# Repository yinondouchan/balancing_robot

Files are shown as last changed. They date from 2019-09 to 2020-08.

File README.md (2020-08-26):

# balancing_robot
A balancing robot trying to become sentient using a Jetson Nano and an Arduino

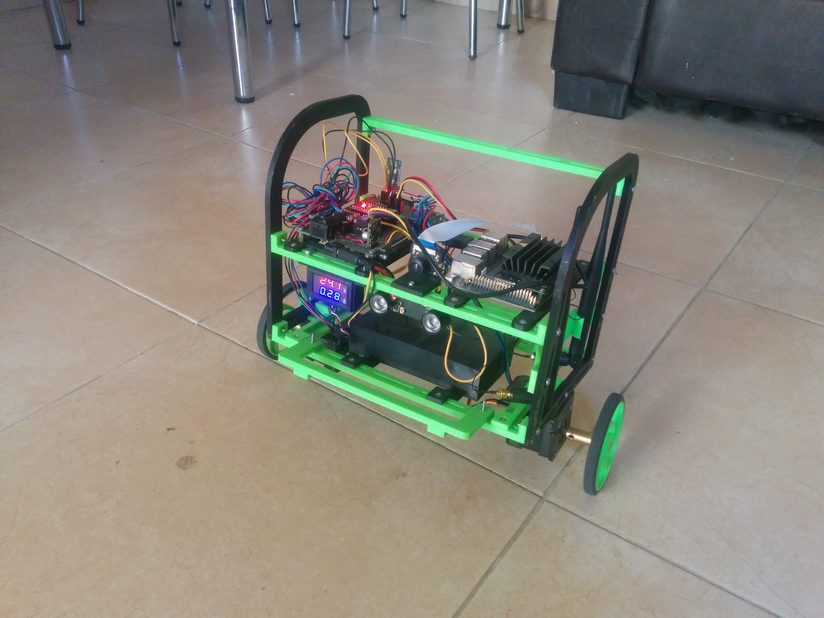
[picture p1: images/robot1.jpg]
my fabulous robot


## Body

The body is made of multiple 3d printed components, held together mostly by nuts and bolts. The components were designed in FreeCAD, converted to STL mesh files, sliced to gcode files and printed.

### Components

Below is a list of the body components printed in a 3d printer. Each component has an stl file in the 3d_models directory.

- 2x side bars (SideBar.stl)
- 5x horizontal beams (HorizontalBeamV4.stl)
- 2x motor bracket connectors (MotorBracketConnectorV5.stl)
- 1x plate for holding the batteries (BatteriesPlate.stl)
- 1x plate for holding the Jetson Nano board (JetsonNanoPlate.stl)
- 1x plate for holding the main board (MainBoardPlateV2.stl)
- 1x bracket for the voltage/current meter (MeterHolder.stl)
- 1x camera holder (CameraHolder.stl)
- (optional) 2x custom pololu 90mm wheels, one is a mirrored version of the other (Pololu90mmWheel2.stl, Pololu90mmWheel2Mirrored.stl)

### Assembly

All components except a few can be assembled using M3 nuts and bolts. The custom Pololu wheels need M4 screws with a length of at least 8mm.

I tried to make the components as modular as possible. That's why I bombarded the side bars and horizontal bars with a 3.5mm diameter slots so it will be possible to mount a wide variety of objects in a wide variety of places on the robot.

Instructions (photos will come):

Skeleton:
- (2x side bars <- 2x horizontal beams) Connect two horizontal beams to the lowest part of the bottom most slots of the side bars.
- (2x side bars <- 2x horizontal beams) Connect two horizontal beams to the lowest part of the second from bottom slots of the side bars.
- (2x side bars <- 1x horizontal beam) Connect one horizontal beam to the lowest part of the upper most slot in the back of the side bar.

Motors:
- (2x side bars, 2x horizontal beams <- 2x motor bracket connectors) Connect the two motor bracket connectors to the side bars and horizontal beams. 

Electronics:
- (2x horizontal beams <- batteries plate) Connect batteries plate to the middle of the two lower horizontal beams.
- (2x horizontal beams <- main board plate) Connect main board plate to the right side of the two middle horizontal beams.
- (2x horizontal beams <- jetson nano plate) Connect jetson nano plate to the left side of the two middle horizontal beams.
- Camera and voltage meter: I mounted the camera to the middle of the forward-middle horizontal beam and the meter in the left side, but you can try different positions.

## Hardware

### Motors
* 2x NEMA 17 stepper motors: https://www.aliexpress.com/item/32855316300.html?spm=a2g0s.9042311.0.0.27424c4dqhugXl
* 2x NEMA 17 steel brackets: https://www.aliexpress.com/item/32812576981.html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,searchweb201602_9,searchweb201603_52

### Motor control
* 2x TB67S249FTG stepper motor drivers: https://www.pololu.com/product/3096

### Wheels
* Alternative A:
  * 2x Pololu 90mm wheels: https://www.pololu.com/product/1438
  * 2x Pololu universal mounting hubs for 5mm shaft and M3 screws: https://www.pololu.com/product/1998
* Alternative B (Using some of the components in alternative A):
  * 2x 5mm hex couplers: https://www.aliexpress.com/item/32959682575.html?spm=a2g0s.9042311.0.0.27424c4docg9sb
  * 3d print a plastic wheel compatible to the above hex coupler and mount the tires of the aforementioned Pololu 90mm wheels on them. This is what I did and I will send the STL file for those wheels.

I initially used alternative A but I found out it does not withstand the robot's loads very well (in my case sharp turns and collisions at 15 km/h) so I moved to alternative B. 

### Microcontrollers and computers
* 1x Fake Arduino Nano board: https://www.aliexpress.com/item/32607801066.html?spm=a2g0s.9042311.0.0.27424c4dqhugXl
* 1x NVIDIA Jetson Nano board: https://www.amazon.com/NVIDIA-Jetson-Nano-Developer-Kit/dp/B07PZHBDKT

### Energy
* 2x battery holders, each for three 18650 li-ion batteries: https://www.aliexpress.com/item/32847696147.html?spm=a2g0s.9042311.0.0.27424c4dqhugXl
* 6x 18650 batteries (Sanyo NCR18650GA 3500mAh 10A batteries): https://www.aliexpress.com/item/32383140026.html?spm=a2g0s.9042311.0.0.61594c4dmH0ZFx
* 1x D24V10F9 9v 1A switching step down voltage regulator: https://www.pololu.com/product/2833
* 1x D24V50F5 5V 5A switching step down voltage regulator: https://www.pololu.com/product/2851

### IMU
* 1x MPU9250 IMU: https://www.aliexpress.com/item/32830071268.html?spm=a2g0s.9042311.0.0.27424c4d3Cm7zj

### Remote control
* 1x HC-05 bluetooth module: https://www.aliexpress.com/item/32806048234.html?spm=a2g0s.9042311.0.0.27424c4d3Cm7zj

### Camera

* Waveshare 160-degree FOV camera with an IMX219 sensor: https://www.waveshare.com/imx219-160-camera.htm

### Miscellaneous
* 1x logic level converter: https://www.aliexpress.com/item/32851503557.html?spm=a2g0s.9042311.0.0.27424c4docg9sb
* 1x voltage and current meter: https://www.aliexpress.com/item/32824062417.html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,searchweb201602_9,searchweb201603_52

## Notes on hardware
* NEMA 17 stepper motors: If you can't obtain those motors you can, of course, try different NEMA 17 motors. I highly reccomend ones with a low resistance and a current rating of at most 2A. Even though a high resistance motor may draw significantly less current (though also a higher voltage), which may prevent the drivers from overheating, such a motor will not retain a high torque at high speeds. The motors I used are rated at 2.2V and 2A and therefore have a resistance of 1.1 Ohm which is very low for such motors.
* Arduino Nano board: Of course you can buy an original, but for me a 2$ fake does everything I need.
* TB67S249FTG stepper motor drivers: Those drivers are relatively expensive because they are Pololu drivers and have the feature of automatically lowering the current consumption of the motors when not needed. A generic chinese A4988 or DRV8835 will definitely do the work, though you may need to wire them differently and change the microstepping settings in the firmware. Link to the suggested alternative drivers: https://www.aliexpress.com/item/32963690420.html?spm=a2g0s.9042311.0.0.27424c4docg9sb
* Battery holders: In order to have 24V input voltage I daisy chained the two battery holders. I don't think it's a good idea even though it worked well up until now. Moreover, if you will need to recharge you will have to manually remove all the batteries and put them in a charger. Therefore, I instead recommend buying a 6s1p battery pack with a BMS instead. I plan to make a battery pack of my own (or buy one) and replace this hack.
* 18650 batteries: Of course you can use other batteries. Just beware of counterfeits and make sure they can deliver at least 5A of continuous current. I measured the capacity of the batteries I bought from the link I gave and indeed their capacity was 3500 mAh so I recommend buying from them.
* While the camera noted above is supported by the Jetson Nano board, there are many cameras (and possibly other devices) that are not supported by the Jetson Nano. One example of an unsupported device is a V1 Raspberry PI camera (based on an ov5647 sensor) - it will simply not work (unless you want to compile the ov5647 driver as a loadable kernel module...). Therefore, when trying new devices double check that the Jetson Nano supports them.

## Wiring

TODO

## Software

### Low level controller (Arduino Nano)

#### Inputs and outputs
The low level controller's main responsibility is to balance the robot given the user's input (if there is any). In the current implementation the user inputs are:

* linear velocity
* turn rate
* online parameter tuning (will be discussed later)
* emergency stop
* linear velocity remote control sensitivity

Given those inputs, the low level controller controls the velocities of the two motors.

#### Block diagram
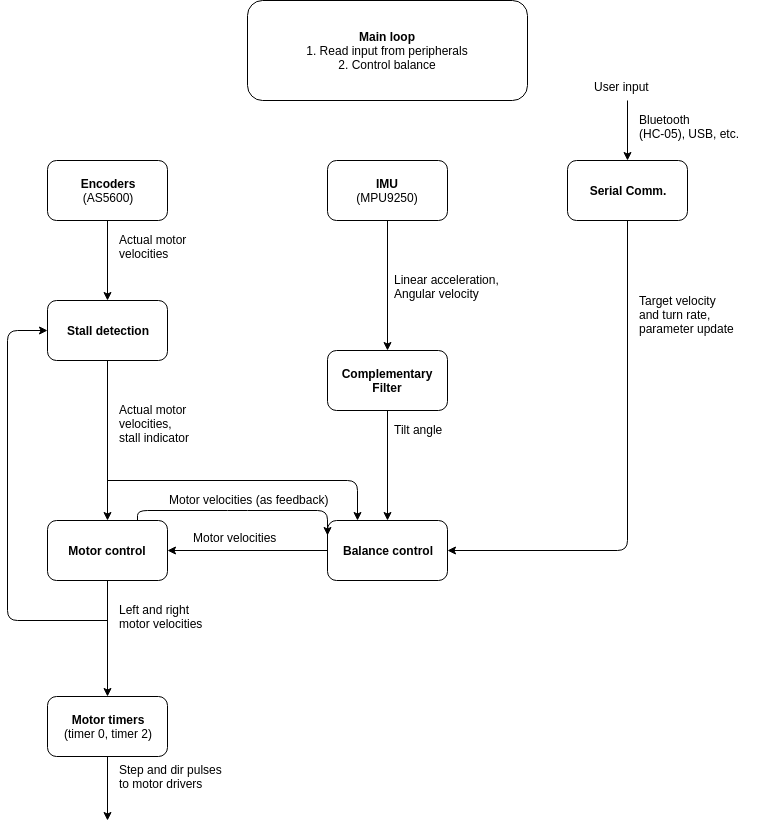
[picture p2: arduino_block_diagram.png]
low_level_controller Low level controller


### High level controller (Jetson Nano)

The high level controller also contains a GPU and is therefore capable of running even deep learning algorithms. For the implemented software refer to https://github.com/yinondouchan/balancing_robot_sw

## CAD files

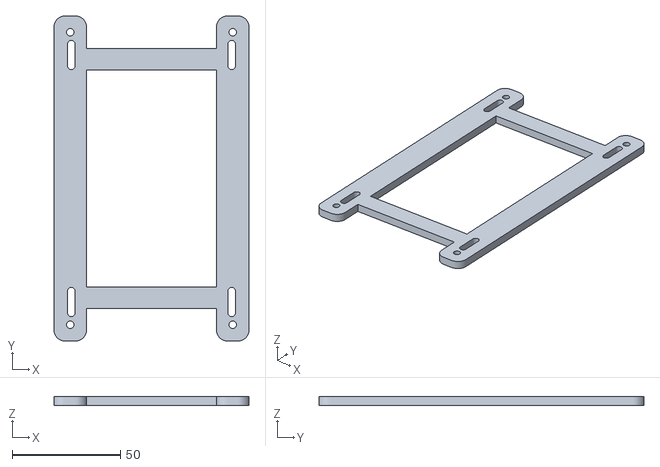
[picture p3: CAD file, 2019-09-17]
3d_models/MainBoardPlateV2.stl
90.0 x 150.0 x 4.00

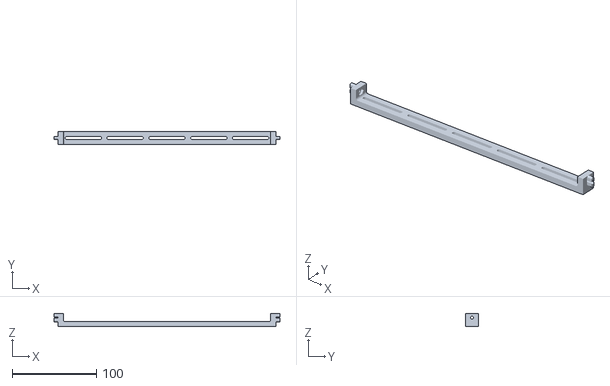
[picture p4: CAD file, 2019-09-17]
3d_models/HorizontalBeamV4.stl
268.0 x 15.0 x 16.0

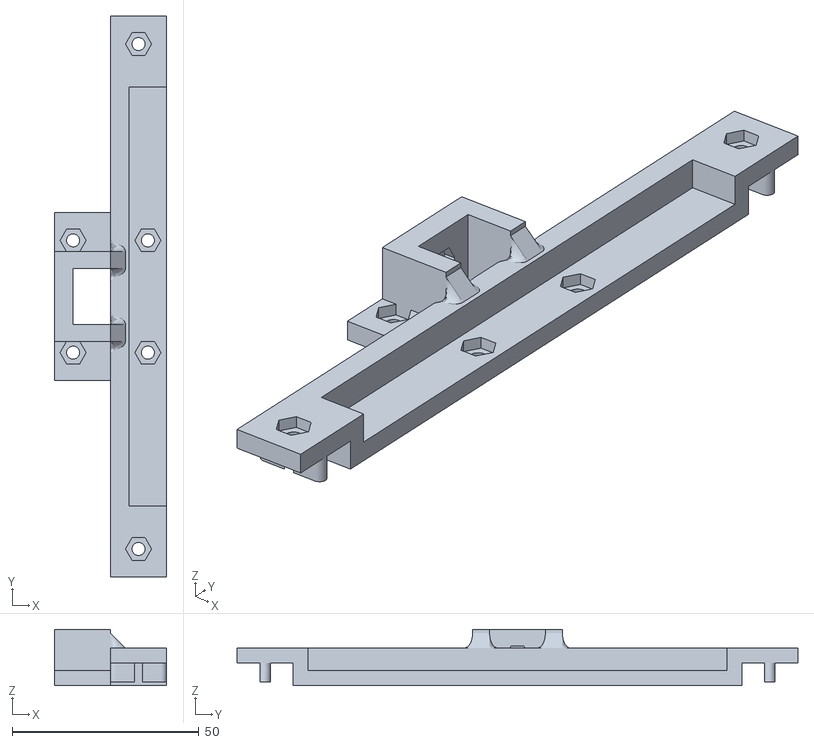
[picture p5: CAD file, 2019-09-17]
3d_models/MotorBracketConnectorV5.stl
30.0 x 150.0 x 15.0

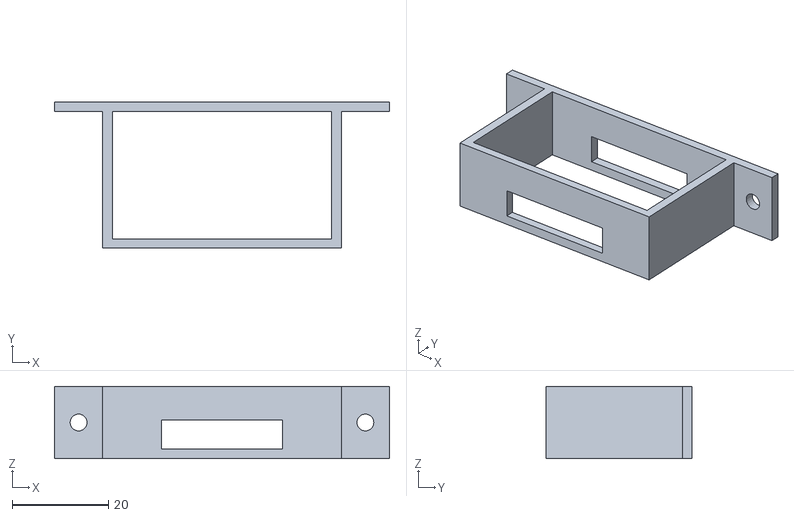
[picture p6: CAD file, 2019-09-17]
3d_models/MeterHolder.stl
69.5 x 30.4 x 15.0

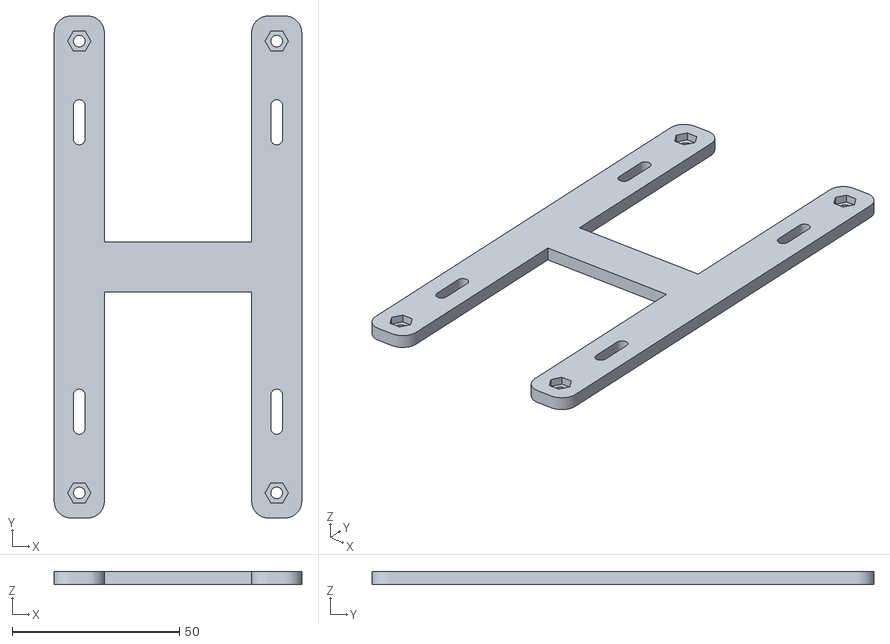
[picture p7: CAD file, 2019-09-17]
3d_models/JetsonNanoPlate.stl
74.0 x 150.0 x 4.00

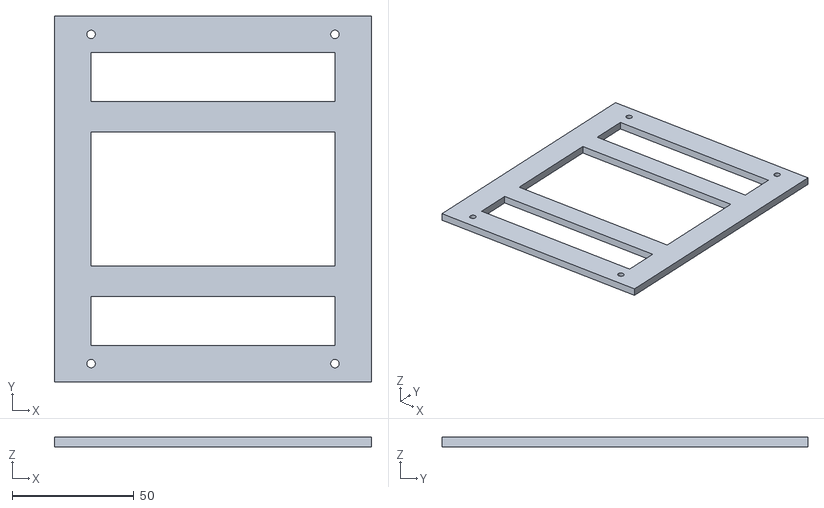
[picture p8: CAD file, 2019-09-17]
3d_models/BatteriesPlate.stl
130.0 x 150.0 x 4.00

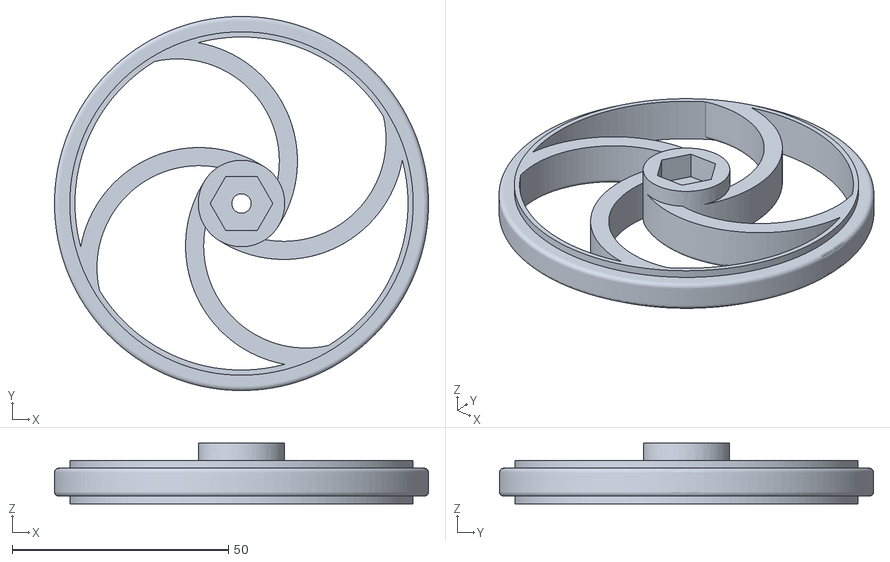
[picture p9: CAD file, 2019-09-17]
3d_models/Pololu90mmWheel2.stl
86.5 x 86.5 x 14.0

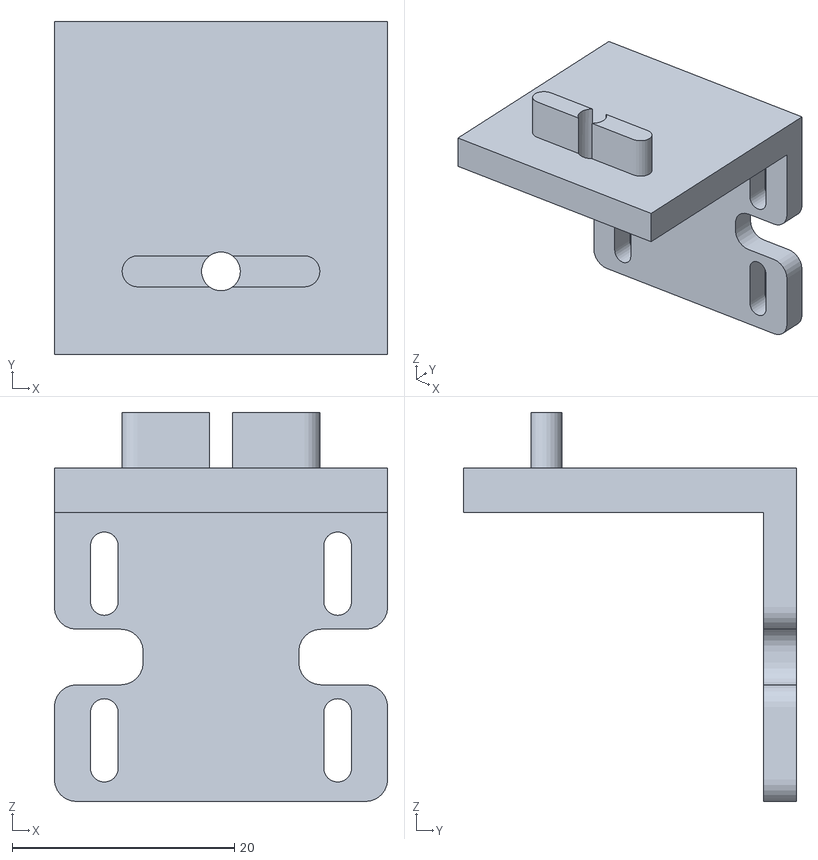
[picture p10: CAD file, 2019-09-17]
3d_models/CameraHolder.stl
30.0 x 30.0 x 35.0

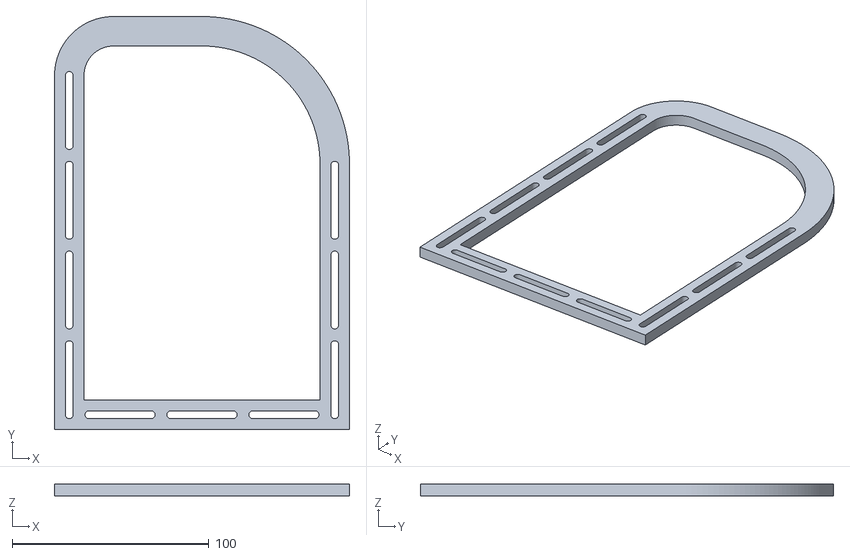
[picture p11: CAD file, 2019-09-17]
3d_models/SideBar.stl
150.0 x 210.0 x 6.00

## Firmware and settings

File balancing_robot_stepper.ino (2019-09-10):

/*
 * Main file for the balancing robot.
 */

#include <Arduino.h>

extern "C"
{
  #include "avr_i2c.h"
}

#include <mpu9250.h>
#include "imu.h"
#include "serial_comm.h"
#include "config.h"

// motor index
#define LEFT_MOTOR 0
#define RIGHT_MOTOR 1

// motor direction
#define DIRECTION_FORWARD 0
#define DIRECTION_BACKWARD 1

// microstepping modes
#define STEP_MODE_FULL 1
#define STEP_MODE_HALF 2
#define STEP_MODE_QUARTER 4
#define STEP_MODE_EIGHTH 8
#define STEP_MODE_SIXTEENTH 16
#define STEP_MODE_THIRTY_TWOTH 32
#define STEP_MODE_AUTO 0    // automatic microstepping selection

// how many timer interrups to count until main loop is triggered
#define LOOP_COUNTER_DIVISOR 40

// main loop time interval in microseconds
#define DT_MICROS 5000

// main loop time interval in seconds
#define DT_SECONDS 0.005

// clock prescaler for the timers responsible for the stepper motors (timer 0 and timer 2)
#define STEP_TIMER_CLOCK_PRESCALER 8

// number of full steps per motor revolution
#define FULL_STEPS_PER_REV 200

// left motor step and direction pins
#define LEFT_MOTOR_STEP_PIN 4
#define LEFT_MOTOR_DIR_PIN 2

// left motor microstepping pins. Actual microstepping values depend on the motor driver used
#define LEFT_MOTOR_MS1_PIN 6
#define LEFT_MOTOR_MS2_PIN 5
#define LEFT_MOTOR_MS3_PIN 9

// left motor encoder pin
#define LEFT_MOTOR_ENCODER_PIN A1

// right motor step and direction pins
#define RIGHT_MOTOR_STEP_PIN 8
#define RIGHT_MOTOR_DIR_PIN 7

// right motor microstepping pins. Actual microstepping values depend on the motor driver used
#define RIGHT_MOTOR_MS1_PIN 11
#define RIGHT_MOTOR_MS2_PIN 12
#define RIGHT_MOTOR_MS3_PIN 100

// right motor encoder pin
#define RIGHT_MOTOR_ENCODER_PIN A0

// number of encoder values per full revolution of the motor
#define ENCODER_FULL_SCALE 1024

// velocity difference threshold for triggering the stall detection and handling mechanism
// threshold is in units of full-steps/sec between desired velocity and what the encoder reads
#define STALL_SPEED_DIFF_THRESHOLD 200

// the amount of acceleration back to desired velocity given a stall
#define STALL_ACCEL_SPEED 100

// clock speed
#define CLOCK_SPEED_HZ 16000000

// the angle in degrees read from the IMU where it is assumed that the robot is perfectly balanced
#define BALANCE_ANGLE -2.5

// a nice macro for calculating the sign of a number
#define SIGN(x) (((x) > 0) - ((x) < 0))

// maximum acceleration and deceleration in full steps per second
#define MAX_ACCEL 2000
#define MAX_DECCEL 2000

// the IMU
MPU_9250 imu;

// tunable parameters
typedef struct
{
    float angle_pid_p;
    float angle_pid_ang_vel_p;
    float vel_pid_p;
    float vel_pid_i;
    float vel_pid_d;
    float vel_lpf_tc;
    int32_t balance_vel_limit;
    float vel_pid_d2;
    float current_limit;
} parameters_t;

// tunable parameters tags
enum parameter_tlv_tag {
                        ANGLE_PID_P,                // inner PID loop angle proportional component
                        ANGLE_PID_ANG_VEL_P,        // inner PID loop angular velocity proportional component
                        VEL_PID_P,                  // outer PID loop velocity proportional
                        VEL_PID_I,                  // outer PID loop velocity integral
                        VEL_PID_D,                  // outer PID loop velocity derivative
                        VEL_LPF_TC,                 // velocity low-pass filter time constant [microseconds]
                        BALANCE_VEL_LIMIT,          // balancing algorithm velocity limit [full-steps per second]
                        VEL_PID_D2,
                        CURRENT_LIMIT,
                        };

// timer counter for left and right motors
volatile int32_t left_motor_counter;
volatile int32_t right_motor_counter;

// timer for main loop
volatile int32_t loop_counter;

// number of timer compare match interrupts per STEP pulse sent to left motor driver
int32_t left_motor_nticks;

// number of timer compare match interrupts per STEP pulse sent to right motor driver
int32_t right_motor_nticks;

// motor's step velocity in full-steps per second
float left_motor_vel;
float right_motor_vel;

// motor's encoder velocity in full-steps per second
float left_motor_encoder_vel;
float right_motor_encoder_vel;

// previous angle read by encoder
int16_t left_motor_prev_angle;
int16_t right_motor_prev_angle;

// step modes for various stepper motor drivers
#if MOTOR_DRIVER == MOTOR_DRIVER_A4988
const uint8_t step_modes[] = {STEP_MODE_FULL, STEP_MODE_HALF, STEP_MODE_QUARTER, STEP_MODE_EIGHTH, STEP_MODE_SIXTEENTH};
#elif MOTOR_DRIVER == MOTOR_DRIVER_MP6500
const uint8_t step_modes[] = {STEP_MODE_FULL, STEP_MODE_HALF, STEP_MODE_QUARTER, STEP_MODE_EIGHTH};
#elif MOTOR_DRIVER == MOTOR_DRIVER_TB67S249
const uint8_t step_modes[] = {STEP_MODE_FULL, STEP_MODE_HALF, STEP_MODE_QUARTER, STEP_MODE_EIGHTH, STEP_MODE_SIXTEENTH, STEP_MODE_THIRTY_TWOTH};
#endif

// output velocity to motor from balancing algorithm
float balance_point_power;

// filtered and unfiltered velocity error from previous cycle
float prev_vel_error_lpf;
float prev_vel;

// I component of the balancing algorithm's top layer
float bp_i;

// low pass filtered velocity error
float vel_error_lpf;

// true if the robot is upright
bool upright;

// true if the robot is on emergency stop 
bool on_estop;

// true if main loop was already triggered for an iteration
bool main_loop_triggered;

// control velocity after applying acceleration and deceleration constraints
float serial_comm_desired_vel_constrained;

// true if one of the robot's motors are stalled
bool on_stall;

// tunable parameters
parameters_t parameters;

// setup the robot's timers
// timer 0 is used for controlling right stepper motor
// timer 1 is used for controlling main loop
// timer 2 is used for controlling left stepper motor
void setup_timers()
{
    // clear all interrupts
    cli();

    // initialize Timer0 for controlling right stepper motor
    TCCR0A = 0;    // set entire TCCR0A register to 0
    TCCR0B = 0;    // set entire TCCR0B register to 0 
                   // (as we do not know the initial  values)

    // enable output compare interrupt for timer 0
    TIMSK0 |= (1 << OCIE0A);

    // set initial output compare register value for timer 0
    OCR0A = 255;

    // set CTC mode (clear timer on compare-match) and set clock prescaler to 8
    TCCR0A |= _BV(WGM01);
    TCCR0B |= _BV(CS01);

    // initialize Timer1 for main loop - a 7812.5 Hz interrupt rate
    TCCR1A = 0;    // set entire TCCR1A register to 0
    TCCR1B = 0;    // set entire TCCR1B register to 0 
                   // (as we do not know the initial  values)

    // enable overflow interrupt for timer 1
    TIMSK1 |= (1 << TOIE1);

    // set fast PWM mode and set prescaler to 8
    TCCR1A += _BV(WGM10);
    TCCR1B |= _BV(CS11) | _BV(WGM12);

    // initialize Timer2 for controlling left stepper motor
    TCCR2A = 0;    // set entire TCCR2A register to 0
    TCCR2B = 0;    // set entire TCCR2B register to 0 
                   // (as we do not know the initial  values)

    // set initial output compare register value for timer 2
    OCR2A = 255;

    // enable output compare interrupt for timer 0
    TIMSK2 |= (1 << OCIE2A);

    // CTC mode and clock prescaler 8 (same as timer 0)
    TCCR2B |= _BV(CS21);
    TCCR2A |= _BV(WGM21);
    
    // enable global interrupts:
    sei();
}

// overflow interrupt for timer 1 (main loop timer)
ISR(TIMER1_OVF_vect)
{
    // count until loop counter reaches the desired value to trigger the main loop
    loop_counter = (loop_counter >= (LOOP_COUNTER_DIVISOR - 1)) ? 0 : loop_counter + 1;
}

ISR(TIMER2_COMPA_vect)
{
    // called every compare-match and controls pulse frequency
    digitalWrite(LEFT_MOTOR_STEP_PIN, left_motor_counter >= (left_motor_nticks - 1));

    // send pulse every nticks interrupts
    left_motor_counter = (left_motor_counter >= (left_motor_nticks - 1)) ? 0 : left_motor_counter + 1;
}

ISR(TIMER0_COMPA_vect)
{
    // called every compare-match and controls pulse frequency
    digitalWrite(RIGHT_MOTOR_STEP_PIN, right_motor_counter >= (right_motor_nticks - 1));

    // send pulse every nticks interrupts
    right_motor_counter = (right_motor_counter >= (right_motor_nticks - 1)) ? 0 : right_motor_counter + 1;
}

// automatic microstepping mode selection as a function of velocity
uint8_t get_auto_step_mode(float velocity)
{
    // choose the finest microstepping mode where it will be possible to reach this velocity without a too high timer interrupt rate
    uint8_t num_of_step_modes = sizeof(step_modes)/sizeof(step_modes[0]);
    for (int i = (num_of_step_modes - 1); i >= 0; i--)
    {
        int32_t step_mode_nticks_value = CLOCK_SPEED_HZ / (velocity * STEP_TIMER_CLOCK_PRESCALER * step_modes[i] * 128);
        if (step_mode_nticks_value >= 2) return step_modes[i];
    }

    return STEP_MODE_FULL;
}

// set the velocity of a motor with a specific step_mode (full step or microstepping)
void set_velocity(uint8_t motor, float velocity, uint8_t step_mode)
{
    // determine the output pins for the right driver
    uint8_t dir_pin = (motor == LEFT_MOTOR) ? LEFT_MOTOR_DIR_PIN : RIGHT_MOTOR_DIR_PIN;
    uint8_t ms1_pin = (motor == LEFT_MOTOR) ? LEFT_MOTOR_MS1_PIN : RIGHT_MOTOR_MS1_PIN;
    uint8_t ms2_pin = (motor == LEFT_MOTOR) ? LEFT_MOTOR_MS2_PIN : RIGHT_MOTOR_MS2_PIN;
    uint8_t ms3_pin = (motor == LEFT_MOTOR) ? LEFT_MOTOR_MS3_PIN : RIGHT_MOTOR_MS3_PIN;
    
    if (motor == LEFT_MOTOR)
    {
        // write direction
        digitalWrite(LEFT_MOTOR_DIR_PIN, velocity < 0 ? DIRECTION_BACKWARD: DIRECTION_FORWARD);

        // assume actual motor velocity equals to desired velocity
        left_motor_vel = velocity;
        velocity = abs(velocity);

        // determine step mode
        if (step_mode == STEP_MODE_AUTO) step_mode = get_auto_step_mode(velocity);
        
        // write stepping mode for left motor
        if (step_mode == STEP_MODE_FULL)
        {
            digitalWrite(LEFT_MOTOR_MS1_PIN, LOW);
            digitalWrite(LEFT_MOTOR_MS2_PIN, LOW);
            digitalWrite(LEFT_MOTOR_MS3_PIN, HIGH);
        }
        else if (step_mode == STEP_MODE_HALF)
        {
            digitalWrite(LEFT_MOTOR_MS1_PIN, LOW);
            digitalWrite(LEFT_MOTOR_MS2_PIN, HIGH);
            digitalWrite(LEFT_MOTOR_MS3_PIN, LOW);
        }
        else if (step_mode == STEP_MODE_QUARTER)
        {
            digitalWrite(LEFT_MOTOR_MS1_PIN, LOW);
            digitalWrite(LEFT_MOTOR_MS2_PIN, HIGH);
            digitalWrite(LEFT_MOTOR_MS3_PIN, HIGH);
        }
        else if (step_mode == STEP_MODE_EIGHTH)
        {
            digitalWrite(LEFT_MOTOR_MS1_PIN, HIGH);
            digitalWrite(LEFT_MOTOR_MS2_PIN, LOW);
            digitalWrite(LEFT_MOTOR_MS3_PIN, HIGH);
        }
        else if (step_mode == STEP_MODE_SIXTEENTH)
        {
            digitalWrite(LEFT_MOTOR_MS1_PIN, HIGH);
            digitalWrite(LEFT_MOTOR_MS2_PIN, HIGH);
            digitalWrite(LEFT_MOTOR_MS3_PIN, LOW);
        }
        else if (step_mode == STEP_MODE_THIRTY_TWOTH)
        {
            digitalWrite(LEFT_MOTOR_MS1_PIN, HIGH);
            digitalWrite(LEFT_MOTOR_MS2_PIN, HIGH);
            digitalWrite(LEFT_MOTOR_MS3_PIN, HIGH);
        }

        // control step rate of left motor (microsteps per second)
        set_step_rate_left(velocity * step_mode);
    }
    if (motor == RIGHT_MOTOR)
    {
        // write direction
        digitalWrite(RIGHT_MOTOR_DIR_PIN, velocity < 0 ? DIRECTION_BACKWARD: DIRECTION_FORWARD);
        right_motor_vel = velocity;
        velocity = abs(velocity);

        // determine step mode
        if (step_mode == STEP_MODE_AUTO) step_mode = get_auto_step_mode(velocity);
        
        // write stepping mode
        if (step_mode == STEP_MODE_FULL)
        {
            digitalWrite(RIGHT_MOTOR_MS1_PIN, LOW);
            digitalWrite(RIGHT_MOTOR_MS2_PIN, LOW);
            digitalWrite(RIGHT_MOTOR_MS3_PIN, HIGH);
        }
        else if (step_mode == STEP_MODE_HALF)
        {
            digitalWrite(RIGHT_MOTOR_MS1_PIN, LOW);
            digitalWrite(RIGHT_MOTOR_MS2_PIN, HIGH);
            digitalWrite(RIGHT_MOTOR_MS3_PIN, LOW);
        }
        else if (step_mode == STEP_MODE_QUARTER)
        {
            digitalWrite(RIGHT_MOTOR_MS1_PIN, LOW);
            digitalWrite(RIGHT_MOTOR_MS2_PIN, HIGH);
            digitalWrite(RIGHT_MOTOR_MS3_PIN, HIGH);
        }
        else if (step_mode == STEP_MODE_EIGHTH)
        {
            digitalWrite(RIGHT_MOTOR_MS1_PIN, HIGH);
            digitalWrite(RIGHT_MOTOR_MS2_PIN, LOW);
            digitalWrite(RIGHT_MOTOR_MS3_PIN, HIGH);
        }
        else if (step_mode == STEP_MODE_SIXTEENTH)
        {
            digitalWrite(RIGHT_MOTOR_MS1_PIN, HIGH);
            digitalWrite(RIGHT_MOTOR_MS2_PIN, HIGH);
            digitalWrite(RIGHT_MOTOR_MS3_PIN, LOW);
        }
        else if (step_mode == STEP_MODE_THIRTY_TWOTH)
        {
            digitalWrite(RIGHT_MOTOR_MS1_PIN, HIGH);
            digitalWrite(RIGHT_MOTOR_MS2_PIN, HIGH);
            digitalWrite(RIGHT_MOTOR_MS3_PIN, HIGH);
        }

        // control step rate of right motor (microsteps per second)
        set_step_rate_right(velocity * step_mode);
    }
}

// control velocity with a stall detection layer built upon it
void set_velocity_with_stall_detection(int8_t motor, float velocity, uint8_t step_mode)
{
    // velocity difference in full steps between control velocity and encoder velocity
    float actual_vel_error = (motor == LEFT_MOTOR) ? (left_motor_vel - left_motor_encoder_vel) : (right_motor_vel - right_motor_encoder_vel);

    // true if stall detected (velocity difference is higher than the defined threshold)
    on_stall = abs(actual_vel_error) >= STALL_SPEED_DIFF_THRESHOLD;

    if (on_stall)
    {        
        // stall occured - immediately set control velocity to what the encoder read
        if (motor == LEFT_MOTOR) left_motor_vel = left_motor_encoder_vel;
        else right_motor_vel = right_motor_encoder_vel;
    }
    else // no stall
    {
        // calculate difference between desired velocity and actual velocity
        float desired_vel_diff = velocity - ((motor == LEFT_MOTOR) ? left_motor_vel : right_motor_vel);

        // sign of the above difference
        int sign = (desired_vel_diff > 0) - (desired_vel_diff < 0);

        if (abs(desired_vel_diff) <= STALL_ACCEL_SPEED)
        {
            // when velocity difference is small enough equalize between desired difference and actual control difference
            if (motor == LEFT_MOTOR) left_motor_vel = velocity;
            else right_motor_vel = velocity;
        }
        else
        {
            // when velocity difference is still big accelerate towards desired velocity
            if (motor == LEFT_MOTOR) left_motor_vel += STALL_ACCEL_SPEED * sign;
            else right_motor_vel += STALL_ACCEL_SPEED * sign;
        }

        // set the velocity accordingly
        set_velocity(motor, motor == (LEFT_MOTOR) ? left_motor_vel : right_motor_vel, step_mode);
    }
}

// read velocity from an encoder
void read_encoder_velocity(uint8_t motor)
{
    // read the angle
    int16_t new_angle = analogRead((motor == LEFT_MOTOR) ? LEFT_MOTOR_ENCODER_PIN : RIGHT_MOTOR_ENCODER_PIN);

    // calculate encoder angle difference
    float prev_angle = (motor == LEFT_MOTOR) ? left_motor_prev_angle: right_motor_prev_angle;
    int16_t encoder_angle_diff = (new_angle - prev_angle);

    // deal with angle overflow, i.e. transition from ENCODER_FULL_SCALE - 1 to 0 or backwards
    if (abs(encoder_angle_diff) > ENCODER_FULL_SCALE/2)
    {
        // angle_diff should be positive
        if (new_angle < prev_angle) encoder_angle_diff += ENCODER_FULL_SCALE;
        // angle_diff should be negative
        else encoder_angle_diff -= ENCODER_FULL_SCALE;
    }

    // find velocity in encoder steps per second
    float new_motor_encoder_vel = -1000000.0 * (float)encoder_angle_diff / DT_MICROS;
    
    // convert to full-steps per second
    new_motor_encoder_vel = new_motor_encoder_vel * FULL_STEPS_PER_REV / ENCODER_FULL_SCALE;

    if (motor == LEFT_MOTOR)
    {
        // add a low-pass filter
        left_motor_encoder_vel = 0.5 * left_motor_encoder_vel + 0.5 * -new_motor_encoder_vel;

        // set previous angle value
        left_motor_prev_angle = new_angle;
    }
    else
    {
        // add a low-pass filter
        right_motor_encoder_vel = 0.5 * right_motor_encoder_vel + 0.5 * new_motor_encoder_vel;

        // set previous angle value
        right_motor_prev_angle = new_angle;
    }
}

// set pulse rate for left motor driver
void set_step_rate_left(float velocity)
{
    if (velocity == 0)
    {
        // if on standstill set timer so it will run on lowest interrupt rate
        OCR0A = 255;
        left_motor_nticks = 1;
        return;
    }
    
    // determine highest nticks (timer interrupts per step pulse) such that OCR can be of the highest value, yet lower than 256
    int32_t max_n_ticks = max(ceil((float)CLOCK_SPEED_HZ / (256 * 8 * velocity)), 2);
    left_motor_nticks = max_n_ticks;

    // given the nticks calculate the OCR value
    OCR2A = CLOCK_SPEED_HZ / (max_n_ticks * 8 * velocity) - 1;
}

// set pulse rate for right motor driver
void set_step_rate_right(float velocity)
{

    if (velocity == 0)
    {
        // if on standstill set timer so it will run on lowest interrupt rate
        OCR0A = 255;
        right_motor_nticks = 1;
        return;
    }
    
    // determine highest nticks (timer interrupts per step pulse) such that OCR can be of the highest value, yet lower than 256
    int32_t max_n_ticks = max(ceil((float)CLOCK_SPEED_HZ / (256 * 8 * velocity)), 2);
    right_motor_nticks = max_n_ticks;

    // given the nticks calculate the OCR value
    OCR0A = CLOCK_SPEED_HZ / (max_n_ticks * 8 * velocity) - 1;
}
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
void loop()
{
    // 200Hz loop rate
    if (!main_loop_triggered && (loop_counter == 0))
    {
        main_loop_triggered = true;
        
        // read accel and gyro values
        read_accel_and_gyro(&imu);

        // read tilt angle
        compl_filter_read(DT_MICROS);

        // read encoders
        read_encoder_velocity(LEFT_MOTOR);
        read_encoder_velocity(RIGHT_MOTOR);

        // read data from serial
        serial_comm_read();

        // detect when robot is not upright
        if ((cf_angle_x < -55) || (cf_angle_x > 55)) upright = false;
        if (!upright || on_estop)
        {
            // robot is either not upright or emergency stop is on
            
            // disable the motors
            disable_motors();

            // check if robot is upright again
            upright = (cf_angle_x > ((int32_t)BALANCE_ANGLE - 10)) && (cf_angle_x < ((int32_t)BALANCE_ANGLE + 10));

            if (upright) gyro_angle_x = cf_angle_x;

            // reset desired velocity
            serial_comm_desired_vel_constrained = 0;

            // reset motor control variables
            reset_motors();
            return;
        }

        calculate_constrained_control_velocity();

        // filter angular velocity control to avoid those annoying discrete level sounds
        serial_comm_desired_vel_diff_lpf = 0.1 * serial_comm_desired_vel_diff + 0.9 * serial_comm_desired_vel_diff_lpf;

        // main balancing algorithm
        balance_control(serial_comm_desired_vel_constrained, - serial_comm_desired_vel_diff_lpf, DT_MICROS);
    }
    else if (loop_counter != 0)
    {
        main_loop_triggered = false;
    }
}

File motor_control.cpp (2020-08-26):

#include <Arduino.h>

#include "motor_control.h"
#include "encoders.h"
#include "parameters.h"

// timer counter for left and right motors
volatile int32_t left_motor_counter;
volatile int32_t right_motor_counter;

// number of timer compare match interrupts per STEP pulse sent to left motor driver
int32_t left_motor_nticks;

// number of timer compare match interrupts per STEP pulse sent to right motor driver
int32_t right_motor_nticks;

// current hardware prescaler for right and left motor
uint16_t right_motor_hw_prescaler;
uint16_t left_motor_hw_prescaler;

// motor's step velocity in full-steps per second
float motor_control_left_motor_vel;
float motor_control_right_motor_vel;

// true if one of the robot's motors are stalled
bool motor_control_on_stall;

// true of motors are enabled
bool motor_control_motors_enabled;

// how many consecutive rocks left/right motor is stalling
uint16_t left_motor_stall_count;
uint16_t right_motor_stall_count;

// step modes for various stepper motor drivers
#if MC_MOTOR_DRIVER == MOTOR_DRIVER_A4988
const uint8_t step_modes[] = {MC_STEP_MODE_FULL, MC_STEP_MODE_HALF, MC_STEP_MODE_QUARTER, MC_STEP_MODE_EIGHTH, MC_STEP_MODE_SIXTEENTH};
#elif MC_MOTOR_DRIVER == MOTOR_DRIVER_MP6500
const uint8_t step_modes[] = {MC_STEP_MODE_FULL, MC_STEP_MODE_HALF, MC_STEP_MODE_QUARTER, MC_STEP_MODE_EIGHTH};
#elif MC_MOTOR_DRIVER == MOTOR_DRIVER_TB67S249
const uint8_t step_modes[] = {MC_STEP_MODE_FULL, MC_STEP_MODE_HALF, MC_STEP_MODE_QUARTER, MC_STEP_MODE_EIGHTH, MC_STEP_MODE_SIXTEENTH, MC_STEP_MODE_THIRTY_TWOTH};
#endif

// compare match interrupt for controlling left motor
ISR(TIMER2_COMPA_vect)
{
    // called every compare-match and controls pulse frequency
    digitalWrite(MC_LEFT_MOTOR_STEP_PIN, left_motor_counter >= (left_motor_nticks - 1));

    // send pulse every nticks interrupts
    left_motor_counter = (left_motor_counter >= (left_motor_nticks - 1)) ? 0 : left_motor_counter + 1;
}

// compare match interrupt for controlling right motor
ISR(TIMER0_COMPA_vect)
{
    // called every compare-match and controls pulse frequency
    digitalWrite(MC_RIGHT_MOTOR_STEP_PIN, right_motor_counter >= (right_motor_nticks - 1));

    // send pulse every nticks interrupts
    right_motor_counter = (right_motor_counter >= (right_motor_nticks - 1)) ? 0 : right_motor_counter + 1;
}

// initialize motor control module
void motor_control_init()
{
    // set up STEP and DIR pins for left motor
    pinMode(MC_LEFT_MOTOR_STEP_PIN, OUTPUT);
    pinMode(MC_LEFT_MOTOR_DIR_PIN, OUTPUT);
    pinMode(MC_LEFT_MOTOR_MS2_PIN, OUTPUT);
    pinMode(MC_LEFT_MOTOR_NENABLE_PIN, OUTPUT);

    // set up STEP and DIR pins for right motor
    pinMode(MC_RIGHT_MOTOR_STEP_PIN, OUTPUT);
    pinMode(MC_RIGHT_MOTOR_DIR_PIN, OUTPUT);
    pinMode(MC_RIGHT_MOTOR_MS2_PIN, OUTPUT);
    pinMode(MC_RIGHT_MOTOR_NENABLE_PIN, OUTPUT);
  
    // set up left motor
    left_motor_nticks = 0;
    left_motor_counter = 0;
    motor_control_left_motor_vel = 0;
    left_motor_hw_prescaler = 8;

     // set up right motor
    right_motor_nticks = 0;
    right_motor_counter = 0;
    motor_control_right_motor_vel = 0;
    right_motor_hw_prescaler = 8;

    // stall detection
    motor_control_on_stall = false;

    // start with motors disabled.
    motor_control_disable_motors();

    left_motor_stall_count = 0;
    right_motor_stall_count = 0;
}

// set pulse rate for a motor driver
void motor_control_set_step_rate(int8_t motor, float velocity)
{
    if (velocity == 0)
    {
        // if on standstill set timer so it will run on lowest interrupt rate
        if (motor == MC_LEFT_MOTOR)
        {
            OCR2A = 255;
            left_motor_nticks = 1;
        }
        else // motor == MC_RIGHT_MOTOR
        {
            OCR0A = 255;
            right_motor_nticks = 1;
        }
        
        return;
    }
    
    // determine highest nticks (timer interrupts per step pulse) such that OCR can be of the highest value, yet lower than 256
    uint16_t hardware_prescaler = 8;// motor_control_set_highest_hw_prescaler(motor, combined_prescaler);
    int32_t software_prescaler = max(ceil((float)CLOCK_SPEED_HZ / (256 * hardware_prescaler * velocity)), 2);
    //int32_t software_prescaler = max(combined_prescaler / hardware_prescaler, 1) + 1;

    // given the nticks calculate the OCR value
    if (motor == MC_LEFT_MOTOR)
    {
        left_motor_nticks = software_prescaler;
        OCR2A = CLOCK_SPEED_HZ / (software_prescaler * hardware_prescaler * velocity) - 1;
    }
    else // motor == MC_RIGHT_MOTOR
    {
        right_motor_nticks = software_prescaler;
        OCR0A = CLOCK_SPEED_HZ / (software_prescaler * hardware_prescaler * velocity) - 1;
    }
}
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

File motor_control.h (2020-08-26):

#ifndef MOTOR_CONTROL_H
#define MOTOR_CONTROL_H

// enable pins
#define MC_LEFT_MOTOR_NENABLE_PIN A2
#define MC_RIGHT_MOTOR_NENABLE_PIN A3

// left motor step and direction pins
#define MC_RIGHT_MOTOR_STEP_PIN 4
#define MC_RIGHT_MOTOR_DIR_PIN 2

// right motor step and direction pins
#define MC_LEFT_MOTOR_STEP_PIN 8
#define MC_LEFT_MOTOR_DIR_PIN 7

// motor index
#define MC_LEFT_MOTOR 0
#define MC_RIGHT_MOTOR 1

// left motor microstepping pins. Actual microstepping values depend on the motor driver used
#define MC_RIGHT_MOTOR_MS1_PIN 6
#define MC_RIGHT_MOTOR_MS2_PIN 5
#define MC_RIGHT_MOTOR_MS3_PIN 9

// right motor microstepping pins. Actual microstepping values depend on the motor driver used
#define MC_LEFT_MOTOR_MS1_PIN 11
#define MC_LEFT_MOTOR_MS2_PIN 12
#define MC_LEFT_MOTOR_MS3_PIN 10

// motor direction
#define MC_MOTOR_DIRECTION_FORWARD 0
#define MC_MOTOR_DIRECTION_BACKWARD 1

// microstepping modes
#define MC_STEP_MODE_FULL 1
#define MC_STEP_MODE_HALF 2
#define MC_STEP_MODE_QUARTER 4
#define MC_STEP_MODE_EIGHTH 8
#define MC_STEP_MODE_SIXTEENTH 16
#define MC_STEP_MODE_THIRTY_TWOTH 32
#define MC_STEP_MODE_AUTO 0    // automatic microstepping selection

// clock prescaler for the timers responsible for the stepper motors (timer 0 and timer 2)
#define MC_STEP_TIMER_CLOCK_PRESCALER 8

// velocity difference threshold for triggering the stall detection and handling mechanism
// threshold is in units of full-steps/sec between desired velocity and what the encoder reads
#define MC_STALL_SPEED_DIFF_THRESHOLD 400

// the amount of acceleration back to desired velocity given a stall
#define MC_STALL_ACCEL_SPEED 100

// enable stall detection
#define ENABLE_STALL_DETECTION true

// number of consecutive iterations with desired_vel != encoder_vel required to declare a stall
#define MC_STALL_DETECTION_TRIGGER_COUNT 2

extern float motor_control_left_motor_vel;
extern float motor_control_right_motor_vel;

extern bool motor_control_on_stall;

extern bool motor_control_motors_enabled;

// initialize motor control module
void motor_control_init();

// set pulse rate
void motor_control_set_step_rate(int8_t motor, float velocity);

// set highest possible hardware prescaler given a required combined prescaler for maintaining a specific pulse rate
uint16_t motor_control_set_highest_hw_prescaler(int8_t motor, uint16_t combined_prescaler);

// set the velocity of a motor with a specific step_mode (full step or microstepping)
void motor_control_set_velocity(uint8_t motor, float velocity, uint8_t step_mode);

// automatic microstepping mode selection as a function of velocity
uint8_t motor_control_get_auto_step_mode(float velocity);

// reset motor control
void motor_control_reset();

// distable the motors
void motor_control_disable_motors();

// enable the motors
void motor_control_enable_motors();

// control velocity with a stall detection layer built upon it
void motor_control_set_velocity_with_stall_detection(int8_t motor, float velocity, uint8_t step_mode);

#endif // MOTOR_CONTROL_H

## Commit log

2019-03-13 found a good stepper velocity control algorithm
2019-04-05 towards fixing the stupid mistake I did with the DT_MICROS
    [balancing_robot_stepper.ino]
2019-04-09 towards replacing motor driver to TB67S249
2019-09-09 organized imu module
2019-09-11 moved motor control functionality to separate files. have more work to do with motor control
2019-09-13 fixed bug where LEFT_MOTOR and RIGHT_MOTOR were reversed
    [balance_control.cpp, encoders.cpp, encoders.h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]
2019-09-17 added 3d models and modified the firmware a bit
    [BatteriesPlate.stl, CameraHolder.stl, HorizontalBeamV4.stl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]
2019-10-07 towards fixing wrong loop timer (how on earth did it work until now???)
    [balance_control.cpp, balancing_robot.ino, motor_control.cpp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]
2019-10-08 fixed wrong loop timer
    [balance_control.cpp, balancing_robot.ino]
2019-10-08 more efficient loop timer
